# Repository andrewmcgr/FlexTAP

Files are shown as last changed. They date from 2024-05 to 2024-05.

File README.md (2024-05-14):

# FlexTAP

This is an experimental flexure based alternative to the Voron TAP for Z probing with the nozzle, compatible with any toolhead that will mount on an R8 TAP.

FlexTAP has two main advantages:
* it's lighter (27 g approx, vs 91 g for an R8 plastic TAP and 76 g for a Mellow CNC alloy TAP)
* it's cheaper. Less hardware involved, no linear rail, no PCB, no magnets.

Vibration behaviour is no worse than other TAP variants, and may be better on some printers.

Actuation force depends on what filament is used to print it, but is sufficiently low not to mar print beds.

Accuracy is very good, on my printers limited by the Z motion system not the probe.

The design also incorporates the rear toolhead board mounting screw position from the XOL carriage for better toolboard stability if using XOL.

This first release is experimental: it works, produces high quality output (the FlexTAP pictured below was printed on a machine fitted with an earlier iteration), but it has not been run for long enough to determine longevity.

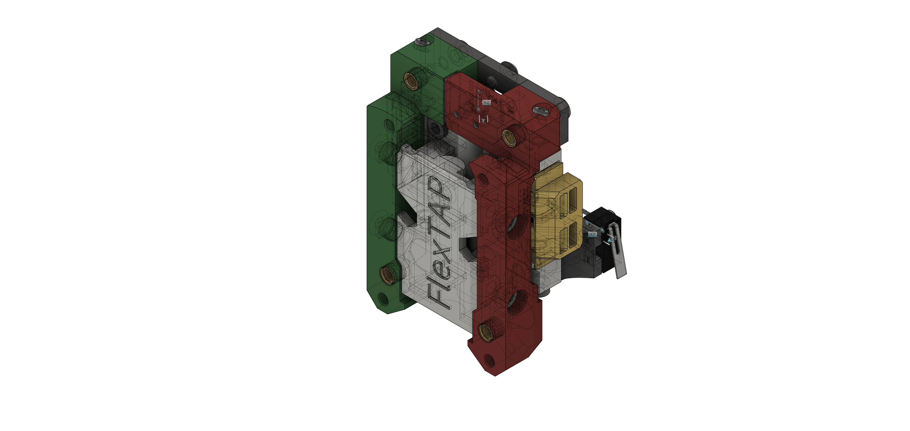
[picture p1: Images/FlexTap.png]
CAD image


# BOM:

* 5x M3x40 screws
* 2x M2x8 to mount the microswitch
* 2x M2x20 BHCS as stiffeners
* 6x standard Voron M3 heatsets
* Omron D2F-01 or D2F-01L (with lever removed) microswitch, wired normally open (the switch is mechanically normally closed, so wire break and misadjustment detection is still available)
* 4x M3x8 to mount to rail carriage
* 2x M3x8 to mount the rear bracket. The bracket provides a center hole compatible with XOL carriage toolhead mounts, but should be installed even if not using that feature.
* 1x M3x8 to mount the endstop bracket, 2x M2x8 to mount the endstop switch, if required. Alternatively, 1x M2 heatset, 1x M2x8, 1x M2 washer to mount the bracket.
* 2x 22mm 4mm OD 3mm ID tubes. PTFE tube is suitable.
* Toolhead mounting screws

# Printing:

* Use ASA by preference. ABS will also work. The flexures were designed and tested with these materials. CF-ASA is suitable, CF-ABS has not been tested. ezPC-CF can also work, but be aware that the parts will need annealing after printing as they will be too brittle otherwise.
* Make sure your profile will handle bridges well and has good layer adhesion.
* Use standard Voron print settings (0.4 mm nozzle, 0.2 mm layer height, at least 3 perimeters, at least 3 top/bottom layers or a shell thickness of 0.8 mm, 45% cubic infill).
* Ensure pressure advance and extrusion multiplier are correctly tuned; any corner bulging will result in poor results.
* Thin walls should be enabled.
* Support for the core is included, STLs are in print orientation.
* v1 had a "Wide" version of the core for CPC rail carriages, v2 will fit these without modification.
* Print and install the XOL bracket even if you will not be using the center screw, it also adds significant rigidity.
* The X endstop bracket is only necessary if you need to mount an endstop microswitch.
* Don't attempt to remove any dropped bridges or other excess material from the flexures themselves. It won't hurt performance, but tool damage to the flexures will.

FlexTAP is not an especially difficult print, if you can print a StealthBurner front section or an R8 Voron TAP, this should present no particular problem.

# Assembly:

See the CAD image and photos. I recommend installing the M2x20 stiffeners and only then installing the heatsets (otherwise the heatsets can prevent the screws going in). One M3x40 goes up from the bottom of the center part, and actuates the switch; this screw may be hard to drive in, I use a power driver.

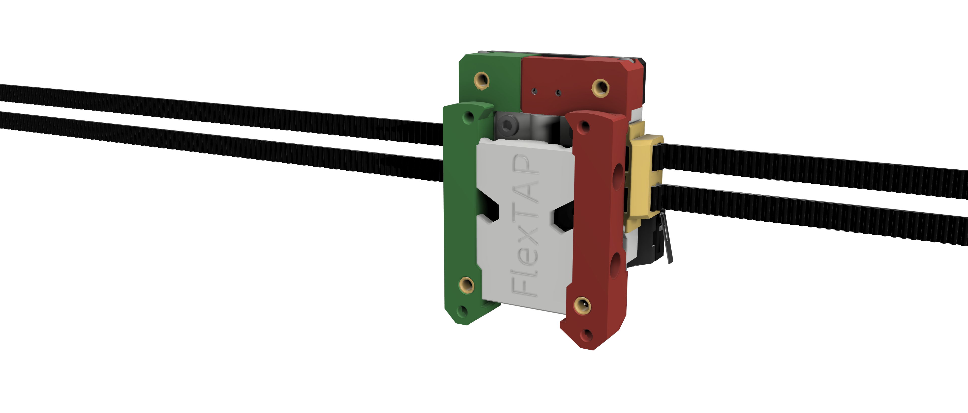
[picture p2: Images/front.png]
Front view render

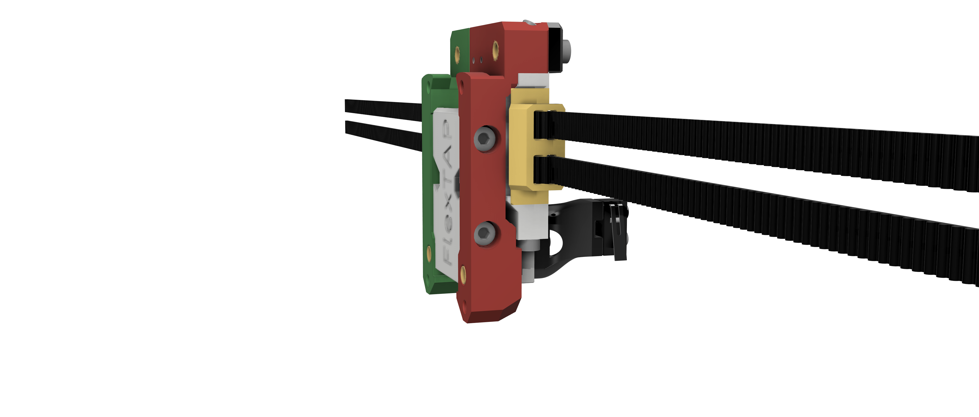
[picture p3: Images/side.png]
Side view render

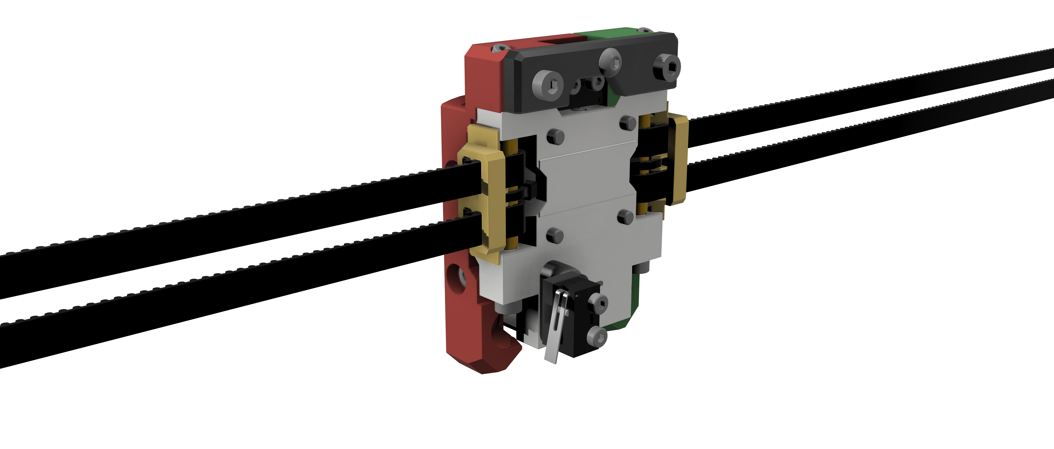
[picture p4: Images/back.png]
Back view render

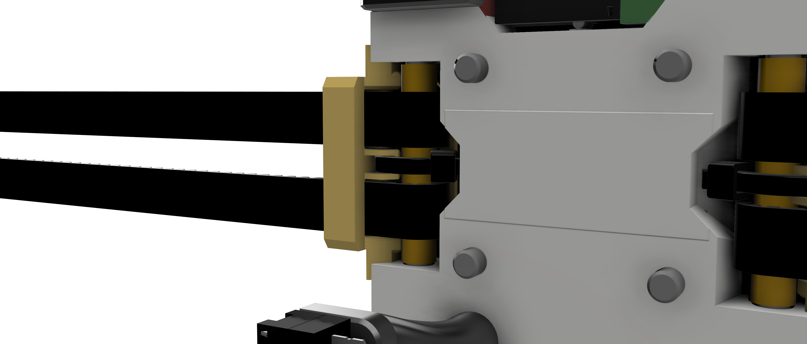
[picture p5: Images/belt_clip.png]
Belt clip


FlexTAP uses Archetype/XOL belt clips. These are installed with the open side facing the rail. Belt enters the slot closest to the rail, is folded back on itself and exits through the same slot, forming a loop around the PTFE tube and screw once installed and locking into the the belt's own teeth. The other slot is for retaining the loose end of the belt if necessary. The narrow slot in the center of the clip is for a small zip tie to hold the assembly together.

@Reth made an [assembly video](https://www.youtube.com/watch?v=gPwkQMZwbeQ) for v1.

# Adjustment:

* Before installation, adjust the center screw so it just barely actuates the switch, verify that the switch can be clicked on and will switch off on its own by pulling the lower belt clamp tabs downward.
* If the switch does not turn off on its own, advance the center screw by about 1/12 turn.

Repeat the adjustment after installing the belt clamps and tensioning the belts but before installing the toolhead (this time pushing the front of the TAP upward).

Once the toolhead is installed and TAP configured, verify correct endstop operation again before attempting to home.

The mechanism takes a number of probes to settle, so it's a good idea to run `probe_accuracy` tests with a total of at least 50 probes before proceeding. Then set Z offset by your favourite method and it should be good to go.

# Acknowledgements:

@zruncho and @chirpy for picking up and running with it, @esoterical for useful discussion, @frix_x for saying "Finally!" when I first mentioned the idea.

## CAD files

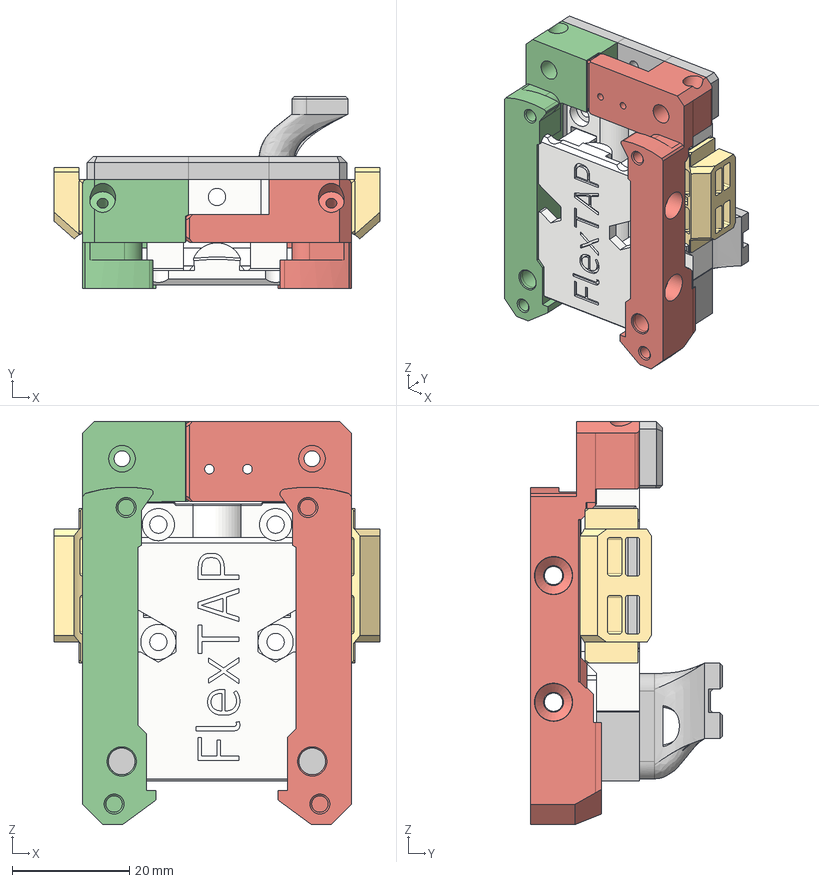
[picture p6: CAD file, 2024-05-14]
CAD/FlexTAP v2.step
55.5 x 32.7 x 68.7 mm
[a]_belt_clamp_6mm_x2
[a]_belt_clamp_6mm_x2(Mirror)
X Endstop Bracket
Frame Left (1)
Frame Right (1)
Back Brace

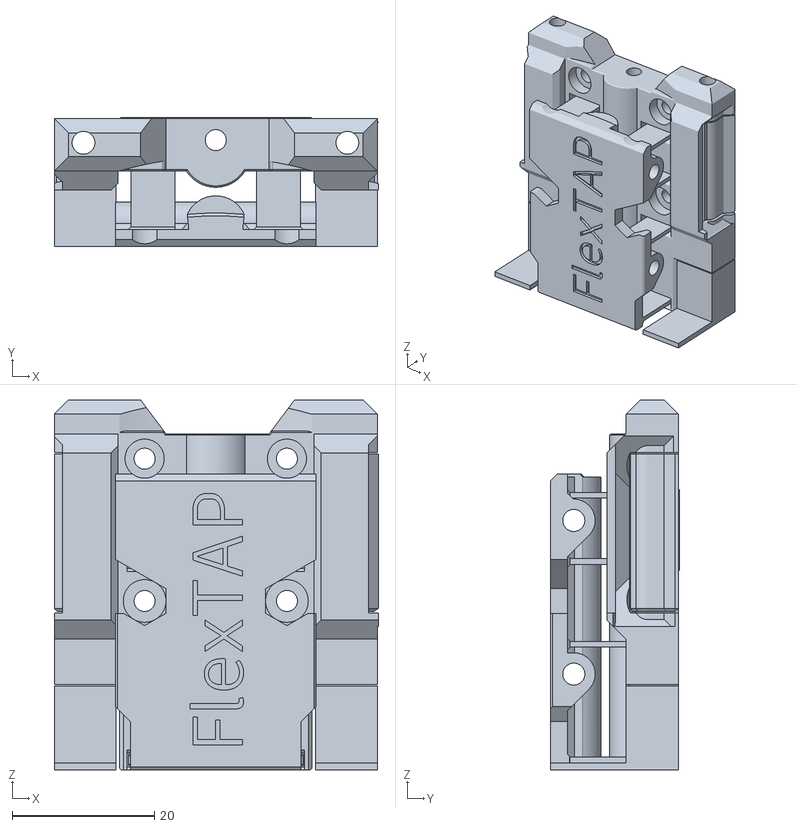
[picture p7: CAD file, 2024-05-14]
STLs/FlexTap_Center.stl
45.6 x 18.2 x 52.0

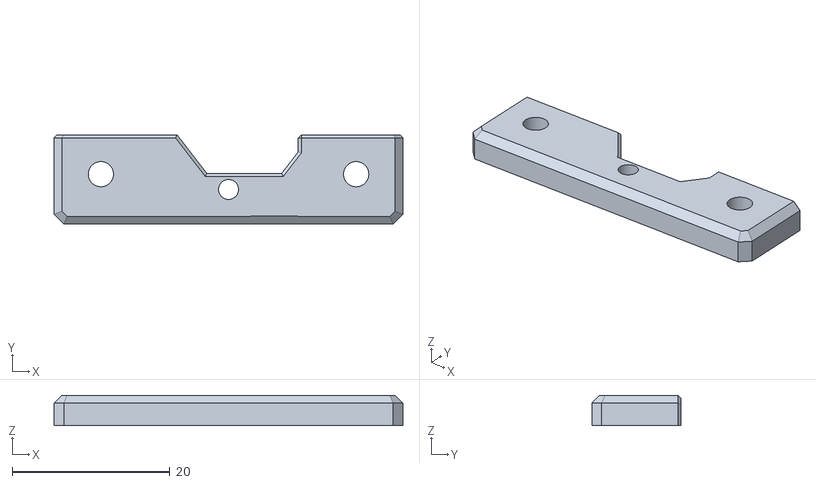
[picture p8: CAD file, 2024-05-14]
STLs/Rear_Bracket.stl
44.3 x 11.3 x 3.86

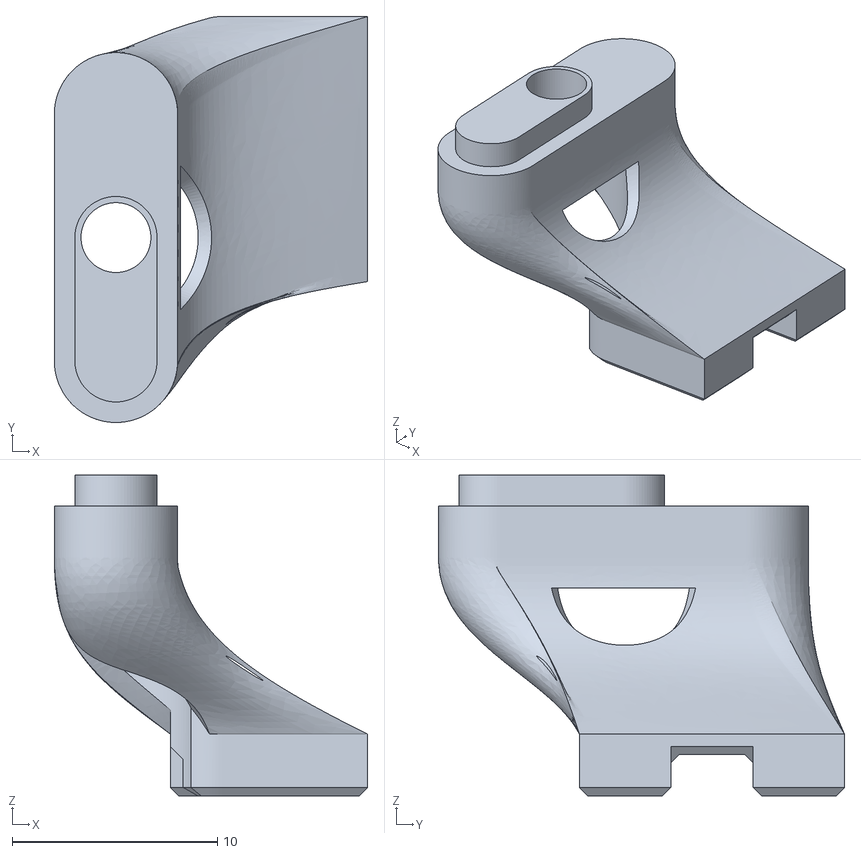
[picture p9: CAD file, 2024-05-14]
STLs/X_Endstop_Bracket.stl
15.3 x 19.8 x 15.6

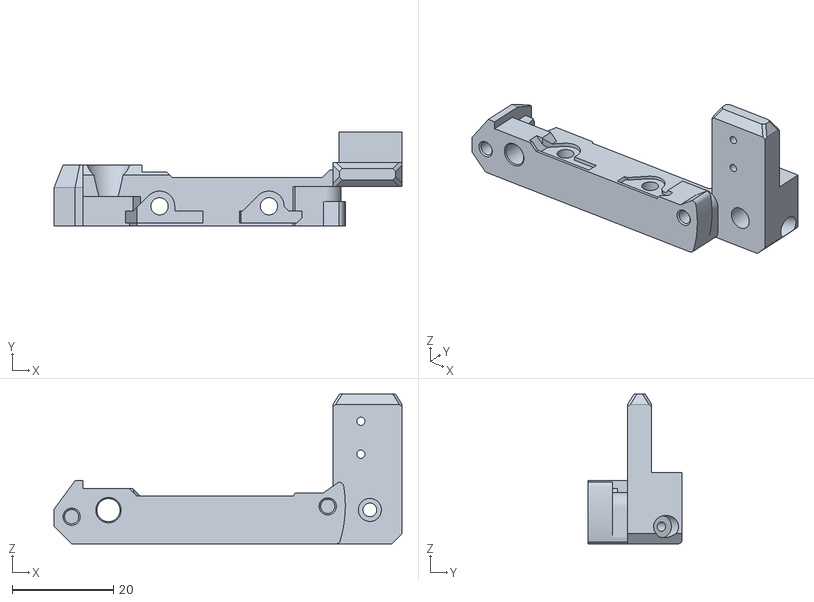
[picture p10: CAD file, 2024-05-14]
STLs/Frame_Right.stl
68.7 x 18.6 x 29.5

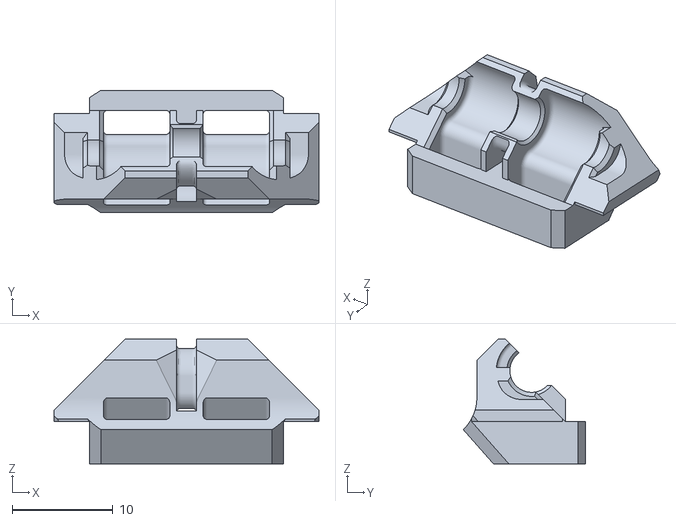
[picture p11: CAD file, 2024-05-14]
STLs/Archetype_RailMount_MGN12-6mm_Clampx2.stl
26.3 x 12.2 x 12.4

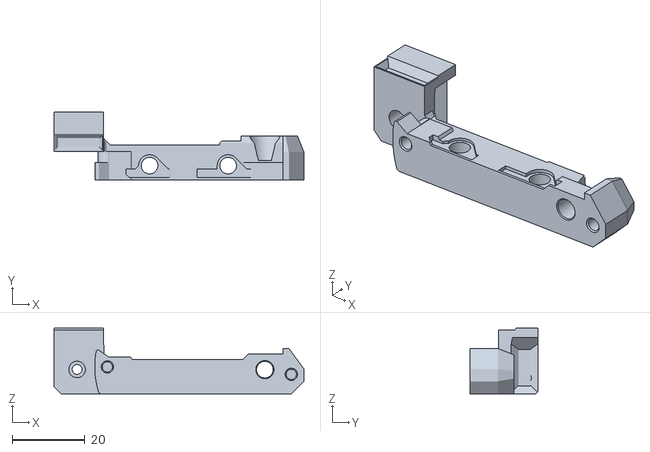
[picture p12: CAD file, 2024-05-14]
STLs/Frame_Left.stl
68.7 x 18.6 x 18.0

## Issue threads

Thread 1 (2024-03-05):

Switchwire version request

akizdor, 2024-03-05:
Please add a version for Voron Switchwire if it is possible.

Fritsbenik, 2024-07-01:
Switchwire isn't possible for the same reason that tap isn't compatible with the Voron Switchwire. The cantilever bed design tilts to much from the pressure of the nozzle to get an accurate reading.

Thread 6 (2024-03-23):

Belt Clip Interference - Sensorless Homing

TheParanoidEngineer, 2024-03-23:
This is such a fascinating design; I truly think it will be the future of TAP.

I have printed it and am impressed with how well it works! However, I noticed that there is an interference with the belt clips before the end of MGN12C carriage travel. This causes issues with senseless homing. This is because the belt clips extend farther to the side than normal TAP. Image shown below:

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

TheParanoidEngineer, 2024-03-25:
I am going to experiment with using an integrated belt clamp on the sensorless homing side:
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

I think this will prevent interference and still allow for adequate tensioning using the left hand side belt clip.

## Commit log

2024-02-27 Initial commit of STLs, images, and CAD
    [Archetype_RailMount_MGN12-6mm_Clampx2.stl, FlexTap_Center.stl, Frame_Left.stl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]
2024-02-28 Minor updates for release:
    * add more hardware to the CAD
    * add a fraction more clearance for the belt clips
    * new CAD image for docs
    [FlexTap_Center.stl, Frame_Left.stl, Frame_Right.stl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]
2024-02-29 Fixed endstop bracket.
    [X_Endstop_Bracket.stl]
2024-03-01 Replace CAD image
2024-03-07 Multiple fixes
    Fix travel limit
    Stronger top belt clip tab
    Lighter flexures
    [FlexTap_Center.stl, Frame_Left.stl, Frame_Right.stl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]
2024-03-07 Updated CAD
2024-03-08 Update supports
    [FlexTap_Center.stl]
2024-03-08 Update CAD
2024-03-11 Avoid binding with larger lower tab.
    [Frame_Left.stl, Frame_Right.stl]
2024-03-11 Fix STL orientation
    [Frame_Left.stl, Frame_Right.stl]
2024-03-13 Make flexures more robust. Wide core version.
    Add belt clamp STEP.
    [FlexTap_Center.stl, FlexTap_Center_Wide.stl]
2024-05-12 Create Archetype v1 clamp v1.step
    Add Archetype v1 clamp CAD
    [Archetype v1 clamp v1.step]
2024-05-12 Add renders
    [Archetype v1 clamp v1.step, Archetype_RailMount_MGN12-6mm_Clampx2.stl, FlexTAP v2.step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]
